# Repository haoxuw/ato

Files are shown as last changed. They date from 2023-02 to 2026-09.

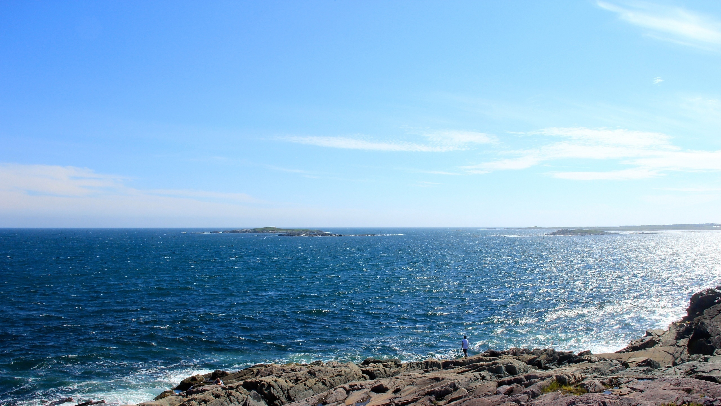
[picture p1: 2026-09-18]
urdf/method.jpg

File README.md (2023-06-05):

# ato

## What is this?

Simple Demo (https://www.youtube.com/watch?v=LdU0oIZtUVM)

See a video demo by clicking the above image.

Ato is an open-source robotic arm that can be built at home with a $200 budget.

## Demos

A 3 segments arm, visualized with dummy servo motors

Assembling a segment

A gripper with sockets to mount servo on its jaw

## Why design another arm

Many existing commercial robotic arms are robust, precise and packed with sensors. They are great, but their $10k~$100k price tag is also prohibitively expansive for the general public.

This arm is designed to be simple and inexpensive, by stacking modularized and interchangeable 3D printable segments. The first 4DoF arm cost around 120 CAD to build, including online orders and shipping costs (to Toronto) of standardized servos, nuts and bolts, and material costs of 3D printing, although excluding the cost for a Raspberry Pi or Arduino, and assumed access to a 3D printing facility or home printer.

A 6 Degrees-of-Freedom (DoF) arm may be built using 3 identical segments. A segment can be assembled by only three 3d printed objects: A bone and 2 mirrored halves of a joint.

Ato is competent for learning, or for proof of concept (PoC) projects. Although it's not built for heavy duty tasks, the 3D printed parts are fairly robust, and cost next to nothing to replace.

## What is in this repo

This repo is composed of 2 sub projects of ato:
 * Mesh: Allow you to build an arm: Modeling and configuration of 3D printable meshes
 * Control: Allow you to control an arm: Joint position space control using a PS4 controller for joint positions
 * ML-based control: Next steps
   * ML-based cartesian position
   * Full trajectories control

list of neat features
 * mesh:
   * Visualize printable STLs, and their compositional parts on a virtual shelf
 * control:
   * Joint space control
   * Cartesian space control using IK
   * Control with PS4 controller
   * Visualized arm simulation using matlab plots
   * Trajectory replay
 * learning -- deprecated due to performance issue
   * Training auto save, modify data/lr and continue
 ## Try it out!

For details visit the README.md in each project folder. Meanwhile here's a bird eye view.

### Build the arm

The arm would be assembled as illustrated:
arm_components_diagram

To manufacture the 3D Printable Structures, you have some options:

#### Download released mesh

STL files are available at the [resources branch](https://github.com/haoxuw/ato/tree/master-resources/printable_mesh).

Meanwhile the CD pipeline keeps the following STL in sync with master branch:
+ [Segment](https://printable-mesh.s3.us-east-2.amazonaws.com/master/SegmentAugmented_printable_mesh.stl)
+ [BoneSeparable](https://printable-mesh.s3.us-east-2.amazonaws.com/master/BoneSeparableVertical_printable_mesh.stl)
+ [BoneSeparablePitchOnly](https://printable-mesh.s3.us-east-2.amazonaws.com/master/pitch_only_BoneSeparableVertical_pitch_only__printable_mesh.stl)
+ [Gripper](https://printable-mesh.s3.us-east-2.amazonaws.com/master/GripperDragonWithServo_printable_mesh.stl)

You can also customize them, see details in ato_mesh/[README.md](https://github.com/haoxuw/ato/blob/master/ato_mesh/README.md)

### 3D print those mesh

Images to be added. Recommended settings to be added.

### Assembling the physical arm

Video to be added.

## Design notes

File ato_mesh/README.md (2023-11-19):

# mesh

## Build pre-defined arm

### Bill of materials (BOM)

### Download pre-defined mesh

STL files are available at the [resources branch](https://github.com/haoxuw/ato/tree/master-resources/printable_mesh).

### Make your customized mesh

Built on top of cadquery, the code in /mesh/ defines the 3D printable meshes of the arm, while strictly and literally practicing object oriented programming.

In case you may want to tweak the structural design, or configuration, such as to alter length or girth. Once your changes passes the continuous integration git actions pipeline (CI), it would be greatly appreciated if you would contribute back to this open source project via pull requests.

#### Make modifications

##### Installation

## Example commands to generate STL files

Tested under ubuntu 20+, python 3.9+, see examples in `ci.yaml`.

### Prerequisites

* python 3.9+
* if first time running, no folder called ./ato_mesh/venv (the script would create).

### Generate STL files

> $ ./ato_mesh/scripts/generate_shelf.sh --export -o ./generated

You sure see logs printed to console as color green. The .stl files would be located under `./ato_mesh/generated/`

## Code architecture

### High-level walk through

To configure an segment with customized length girth etc. Define a new class under segment_configuration.py . Functionality of the variables are [illustrated here](https://github.com/haoxuw/ato/blob/master-resources/images/illustrations/segment_config_diagram.png)
### Naming conventions

## Demo

### Build

### Alternatives
While it's a bad idea, in theory, one may build a theoretical 10-segment arm

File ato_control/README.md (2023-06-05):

# Contorller Manual

This section describes how to control the arm.

## Get Started

### Prerequisites

1. Activate venv and install dependencies
2. If using PS4 controller, connect to bluetooth. Some hardware doesn't work well with Raspberry Pi OS, you may try to connect by holding `Share` + `PS` button.

### Start the Controller
```
./scripts/activate_arm.sh
```

The PS4 controller signals are updated by `/dev/input/js*` on ubuntu. This script would try connect to the lastest connected joystick device. To specify a target input device, e.g. js6, use `./ato_control/scripts/activate_arm.sh -j 6`

## Using a PS4 controller

### Short Story

* 2 Joysticks to control 2 segments, `L1 R1` to swtich targeted segments.
* `L2 R2` to control gripper.
* `Share` to `enable` detailed logging, `Option` to disconnect.
* `Arrow keys` to switch modes.
* `L3` (press left joystick) move to Home positions.
* `R3` to replay a saved trajectory.

### Long Story

Each mode is mapped to an arrow key, via
```
def __update_input_states(self, key, value):
  ...
def __controller_mode_to_button_mapping(self):
  ...
```

Results in mapping:
```
{
    UP: IN_CARTESIAN_MODE,
    RIGHT: IN_JOINT_SPACE_MODE,
    DOWN: IN_SETTING_MODE,
    LEFT: IN_TRAJECTORY_EDITING_MODE,
}
```

## Modes

The controller can be in one of four possible modes, defined by:

```
def controller_modes(self):.
 - IN_CARTESIAN_MODE
   - Under development and disabled -- limited functionality with preformings to be improved
 - IN_JOINT_SPACE_MODE
   - Control each servo motor individually
 - IN_SETTING_MODE
   - Calibrating between physical and logical position of motors, change velocity
 - IN_TRAJECTORY_EDITING_MODE
   - To create a trajectory, either by setting waypoints and pauses, or recording one live.
"""
```

#### IN_CARTESIAN_MODE

Disabled, currently under development, sorry.

#### IN_JOINT_SPACE_MODE

Left joystick to control the 1st segment, right for the 2nd. Pushing vertically for roll, horizontally for pitch.

Press R1, so that left for the 2nd, right for the 3rd. Press again for 3rd and 4th. Press L1 to reverse. 

#### IN_SETTING_MODE

Mainly used for advanced calibration.

#### IN_TRAJECTORY_EDITING_MODE

* `L3` save the trajectory in editting, and reset_trajectory_in_editing buffer
* `Circle (O)` reset_trajectory_in_editing buffer
* `Cross (X)` append the current position as waypoint
* `Triagle` append a pause
* `Square` toggle trajectory segment recording, each segment would be appended to trajectory in editting

## Using a Kyeboard

To be implemented.

# Software Architecture

This package uses the following components to implement control flow of the arm

-- root obj of arm: ArmController
  -- contains: Ps4Joystick
  -- contains: RaspberryPi
  -- contains multiple: ServoInterface
      -- each has reference to the RaspberryPi

## More Example Commands

#### Start arm controller without connecting to RPI and also enable visualization
> $ ./ato_control/scripts/activate_arm.sh

#### To start arm controller to interface with RaspberryPI (RPI), with joystick at /dev/input/js0 (-j 0)
> $ ./ato_control/scripts/activate_arm.sh -j 0

#### If you have ros installed, you can examine the URDF models by

> $ sudo apt-get install libatlas-base-dev -y
> $ ./ato_control/scripts/download_urdf_mesh_stl.sh && roslaunch urdf_tutorial display.launch model:=./urdf/ato_3_seg_270_deg.urdf

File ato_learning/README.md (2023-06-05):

# This package is currently deprecated due to performance issue

# Prerequisites

## Install Cuda GPU support
e.g.

```
$ sudo apt install nvidia-cuda-toolkit
$ sudo apt purge nvidia-*
$ sudo add-apt-repository ppa:graphics-drivers/ppa
$ sudo apt update
$ sudo apt install nvidia-470
```

## Example commands to train inverse kinematics

### Generate training data with the control package
> $ ./ato_control/scripts/activate_arm.sh --generate_training_data 1000000 --training_data_filepath_prefix ~/.ato/training_data

### Start training using the data generated above
> $ ./ato_learning/scripts/training.sh --training_data_filepath_prefix ~/.ato/training_data --max_epochs 256 --depth 12 --width 256 --new_ik

### you can kill the above process anytime, and resume training by
> $ ./ato_learning/scripts/training.sh --training_data_filepath_prefix ~/.ato/training_data --max_epochs 256 --depth 12 --width 256 --fit_ik

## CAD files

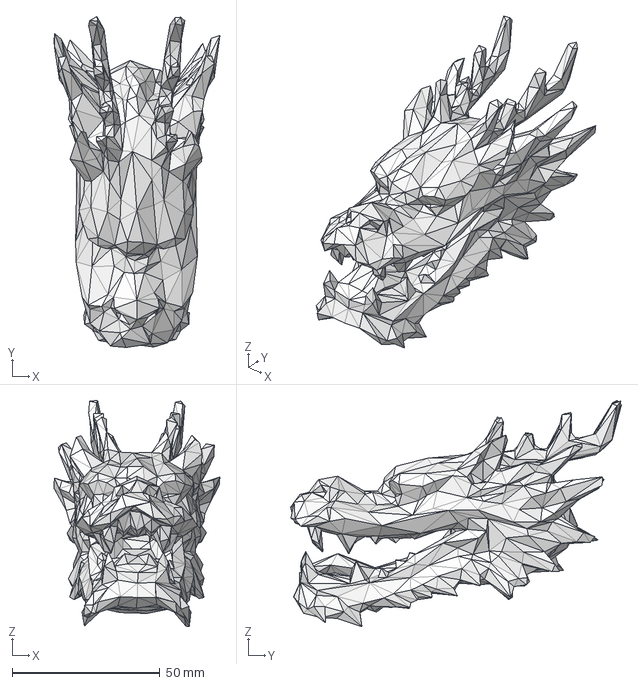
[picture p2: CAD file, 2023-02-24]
ato_mesh/mesh/model_structure/gripper/dragon_head.step
56.1 x 111.9 x 76.5 mm

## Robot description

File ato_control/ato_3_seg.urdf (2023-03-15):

<robot name="ato">
  <link name="base_link">
    <visual>
      <origin rpy="0 0 0" xyz="0 0 0"/>
      <geometry>
      <mesh filename="file:///tmp/BoneAugmented_urdf_mesh.stl"/>
      </geometry>
    </visual>
  </link>

  <joint name="base_link_to_joint_1" type="revolute">
    <axis xyz="0 0 1"/>
    <limit lower="-1.5708" upper="3.14159" effort="1.0" velocity="1.0"/>
    <parent link="base_link"/>
    <child link="joint_1"/>
    <origin xyz="0 0 0" rpy="0 0 0"/>
  </joint>

  <link name="joint_1">
    <visual>
      <origin rpy="0 0 0" xyz="0 0 0"/>
      <geometry>
      <mesh filename="file:///tmp/JointAugmented_urdf_mesh.stl"/>
      </geometry>
    </visual>
  </link>

  <joint name="joint_1_to_bone_1" type="revolute">
    <axis xyz="1 0 0"/>
    <limit lower="-2.26893" upper="2.26893" effort="1.0" velocity="1.0"/>
    <parent link="joint_1"/>
    <child link="bone_1"/>
    <origin xyz="0 0 220" rpy="0 0 0"/>
  </joint>

  <link name="bone_1">
    <visual>
      <origin rpy="0 0 0" xyz="0 0 0"/>
      <geometry>
      <mesh filename="file:///tmp/BoneAugmented_urdf_mesh.stl"/>
      </geometry>
    </visual>
  </link>

  <joint name="bone_1_to_joint_2" type="revolute">
    <axis xyz="0 0 1"/>
    <limit lower="-1.5708" upper="3.14159" effort="1.0" velocity="1.0"/>
    <parent link="bone_1"/>
    <child link="joint_2"/>
    <origin xyz="0 0 0" rpy="0 0 0"/>
  </joint>

  <link name="joint_2">
    <visual>
      <origin rpy="0 0 0" xyz="0 0 0"/>
      <geometry>
      <mesh filename="file:///tmp/JointAugmented_urdf_mesh.stl"/>
      </geometry>
    </visual>
  </link>

  <joint name="joint_2_to_bone_2" type="revolute">
    <axis xyz="1 0 0"/>
    <limit lower="-2.26893" upper="2.26893" effort="1.0" velocity="1.0"/>
    <parent link="joint_2"/>
    <child link="bone_2"/>
    <origin xyz="0 0 220" rpy="0 0 0"/>
  </joint>

  <link name="bone_2">
    <visual>
      <origin rpy="0 0 0" xyz="0 0 0"/>
      <geometry>
      <mesh filename="file:///tmp/BoneAugmented_urdf_mesh.stl"/>
      </geometry>
    </visual>
  </link>

  <joint name="bone_2_to_joint_3" type="revolute">
    <axis xyz="0 0 1"/>
    <limit lower="-1.5708" upper="3.14159" effort="1.0" velocity="1.0"/>
    <parent link="bone_2"/>
    <child link="joint_3"/>
    <origin xyz="0 0 0" rpy="0 0 0"/>
  </joint>

  <link name="joint_3">
    <visual>
      <origin rpy="0 0 0" xyz="0 0 0"/>
      <geometry>
      <mesh filename="file:///tmp/JointAugmented_urdf_mesh.stl"/>
      </geometry>
    </visual>
  </link>

  <joint name="joint_3_to_bone_3" type="revolute">
    <axis xyz="1 0 0"/>
    <limit lower="-2.26893" upper="2.26893" effort="1.0" velocity="1.0"/>
    <parent link="joint_3"/>
    <child link="bone_3"/>
    <origin xyz="0 0 220" rpy="0 0 0"/>
  </joint>

  <link name="bone_3">
    <visual>
      <origin rpy="0 0 0" xyz="0 0 0"/>
      <geometry>
      <mesh filename="file:///tmp/GripperDragonWithServo_urdf_mesh.stl"/>
      </geometry>
    </visual>
  </link>

  <joint name="bone_3_to_endeffector" type="fixed">
    <parent link="bone_3"/>
    <child link="endeffector_link"/>
    <origin xyz="0 0 147" rpy="0 0 0"/>
  </joint>

  <link name="endeffector_link">
    <visual>
      <origin rpy="0 0 0" xyz="0 0 0"/>
      <geometry>
       <box size="1 2 3"/>
      </geometry>
    </visual>
  </link>
</robot>

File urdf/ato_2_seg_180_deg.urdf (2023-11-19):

<robot name="ato">
  <link name="bone_0">
    <visual>
      <origin rpy="0 0 0" xyz="0 0 0"/>
      <geometry>
      <mesh filename="file:///tmp/pitch_range_180/BoneAugmented_urdf_mesh.stl"/>
      </geometry>
    </visual>
    <inertial>
      <mass value="0.0"/>
      <inertia ixx="0.0" ixy="0.0" ixz="0.0" iyy="0.0" iyz="0.0" izz="0.0"/>
    </inertial>
  </link>

  <joint name="bone_0_to_joint_1" type="revolute">
    <axis xyz="0 0 1"/>
    <limit lower="-1.5708" upper="1.5708" effort="1.0" velocity="1.0"/>
    <parent link="bone_0"/>
    <child link="joint_1"/>
    <origin xyz="0 0 0" rpy="0 0 0"/>
  </joint>

  <link name="joint_1">
    <visual>
      <origin rpy="0 0 0" xyz="0 0 0"/>
      <geometry>
      <mesh filename="file:///tmp/pitch_range_180/JointAugmented_urdf_mesh.stl"/>
      </geometry>
    </visual>
  </link>

  <joint name="joint_1_to_bone_1" type="revolute">
    <axis xyz="1 0 0"/>
    <limit lower="-1.48353" upper="1.48353" effort="1.0" velocity="1.0"/>
    <parent link="joint_1"/>
    <child link="bone_1"/>
    <origin xyz="0 0 200" rpy="0 0 0"/>
  </joint>

  <link name="bone_1">
    <visual>
      <origin rpy="0 0 0" xyz="0 0 0"/>
      <geometry>
      <mesh filename="file:///tmp/pitch_range_180/BoneAugmented_urdf_mesh.stl"/>
      </geometry>
    </visual>
  </link>

  <joint name="bone_1_to_joint_2" type="revolute">
    <axis xyz="0 0 1"/>
    <limit lower="-1.5708" upper="1.5708" effort="1.0" velocity="1.0"/>
    <parent link="bone_1"/>
    <child link="joint_2"/>
    <origin xyz="0 0 0" rpy="0 0 0"/>
  </joint>

  <link name="joint_2">
    <visual>
      <origin rpy="0 0 0" xyz="0 0 0"/>
      <geometry>
      <mesh filename="file:///tmp/pitch_range_180/JointAugmented_urdf_mesh.stl"/>
      </geometry>
    </visual>
  </link>

  <joint name="joint_2_to_endeffector" type="revolute">
    <axis xyz="1 0 0"/>
    <limit lower="-1.48353" upper="1.48353" effort="1.0" velocity="1.0"/>
    <parent link="joint_2"/>
    <child link="endeffector"/>
    <origin xyz="0 0 200" rpy="0 0 0"/>
  </joint>

  <link name="endeffector">
    <visual>
      <origin rpy="0 0 0" xyz="0 0 0"/>
      <geometry>
      <mesh filename="file:///tmp/pitch_range_180/GripperDragonWithServo_urdf_mesh.stl"/>
      </geometry>
    </visual>
  </link>

  <joint name="endeffector_to_dummy_object" type="revolute">
    <axis xyz="1 0 0"/>
    <limit lower="0" upper="0" effort="1.0" velocity="1.0"/>
    <parent link="endeffector"/>
    <child link="dummy_object_link"/>
    <origin xyz="0 0 147" rpy="0 0 0"/>
  </joint>

  <link name="dummy_object_link">
    <visual>
      <origin rpy="0 0 0" xyz="0 0 0"/>
      <geometry>
       <box size="1 2 3"/>
      </geometry>
    </visual>
  </link>
</robot>

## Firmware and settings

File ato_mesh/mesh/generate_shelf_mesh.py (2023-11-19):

# This software is forever free for personal and educational usage,

# Copyright (c) 2023, ATOBOT CORP. (1000399600) and/or its affiliates,
# distributed under a multi-licensing model, available for Proprietary and GPL.

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
import argparse
import logging

from mesh.configuration import arm_configuration, segment_configuration
from mesh.cq_lib import cq_mesh_shelf
from mesh.model_structure.arm import arm, mount
from mesh.model_structure.gripper import (
    gripper_dragon_with_servo,
    gripper_tri_sticks_with_servo,
)
from mesh.model_structure.mechanical_parts import (
    allocated_motors,
    bolt,
    horn_arm_25T,
    horn_disk_ds5160,
    horn_disk_nema17,
    motor_servo,
    motor_stepper,
)
from mesh.model_structure.segment import (
    bone_augmented,
    bone_separable,
    bone_separable_vertical,
    joint_augmented,
    segment_augmented,
)
from mesh.model_structure.segment.abstractions import (
    bone_abstract,
    joint_abstract,
    segment_abstract,
)
from mesh.model_structure.toys import gripper_dragon_on_wheels, wheels


def get_args():
    parser = argparse.ArgumentParser()
    parser.add_argument(
        "--abstract",
        action="store_true",
        help="If only print the abstract objects, this would remove functional components such as bolt sockets, motor holder etc.",
    )
    parser.add_argument(
        "--pitch_range_180",
        action="store_true",
        help="If generate joints with pitch ranges of 0~180 or 0~270",
    )
    parser.add_argument(
        "--joint_polygon_sides",
        type=int,
        default=-1,
        help="If generate polygon joint, round if -1",
    )
    parser.add_argument(
        "--all", action="store_true", help="If export all models on shelf"
    )
    parser.add_argument(
        "--no_default",
        action="store_true",
        help="If not to print the default printable models, which includes a complete segment, separable bone, and gripper",
    )
    parser.add_argument(
        "--toys", action="store_true", help="If print the random selection of odd toys"
    )
    parser.add_argument("--bolt", action="store_true", help="If print bolt")
    parser.add_argument("--gripper", action="store_true", help="If print gripper")
    parser.add_argument("--motor", action="store_true", help="If print motor")
    parser.add_argument("--parts", action="store_true", help="If print whole")
    parser.add_argument("--bone", action="store_true", help="If print bone")
    parser.add_argument("--mount", action="store_true", help="If print mount")
    parser.add_argument(
        "--arm_include_motor_mesh",
        action="store_true",
        help="If print an assembled arm with motor_mesh",
    )
    parser.add_argument("--stepper", action="store_true")
    parser.add_argument("--servo", action="store_true")
    parser.add_argument("--arm", action="store_true", help="If print an assembled arm")

    parser.add_argument(
        "--arm10", action="store_true", help="If print an assembled 10-segment arm"
    )
    parser.add_argument(
        "--cylinder", action="store_true", help="If use cylinder roll holder"
    )
    parser.add_argument(
        "--separable_bone", action="store_true", help="If generate separable bone"
    )
    parser.add_argument(
        "--separable_bone_pitch_only",
        action="store_true",
        help="If only generate pitch separable bone",
    )
    parser.add_argument(
        "--gripper_servo_use_shaft_bolt",
        action="store_true",
        help="If generate installation space for a shaft bolt for the gripper",
    )
    parser.add_argument(
        "--tighten_bolt_socket",
        action="store_true",
        help="If print bolt socket that are smaller than bolt diameter, so that it the helix screws into the model.",
    )
    parser.add_argument(
        "--nozzle_diameter",
        type=float,
        default=0.4,
        help="The nozzle diameter used for 3D printing. This value will be used in asserts, to make sure intentional gaps are appropriate in relations to nozzle diameter.",
    )
    parser.add_argument(
        "--horn_bolt_length_override",
        type=int,
        default=None,
        help="If use a specified horn_bolt_length",
    )
    parser.add_argument(
        "--bone_length",
        type=int,
        default=57,
        help="Defaults bone length.",
    )
    parser.add_argument(
        "--export", action="store_true", help="If export printable models on shelf"
    )
    parser.add_argument(
        "--export_all", action="store_true", help="If export all models on shelf"
    )
    parser.add_argument(
        "-o",
        "--out_dir",
        dest="out_dir",
        type=str,
        default="./generated",
        help="Where to put the generated resources",
    )
    parser.add_argument(
        "--no_axes",
        action="store_true",
        help="If not visualize axes (distinguished by length X:1 Y:2 Z:3)",
    )
    parser.add_argument(
        "--no_shelf",
        action="store_true",
        help="If not visualize shelf (i.e. collection of all the mesh)",
    )
    return parser.parse_args()


def add_models(cq_meshes, args):
    logging.info("Adding models to shelf for display and export...")
    if not args.stepper or args.servo:
        actuator_type = segment_configuration.MotorType.SERVO
    else:
        actuator_type = segment_configuration.MotorType.STEPPER

    segment_configs = segment_configuration.SegmentConfigs(
        bone_length=args.bone_length,
        actuator_type=actuator_type,
        joint_polygon_sides=args.joint_polygon_sides,
        pitch_range_180=args.pitch_range_180,
        nozzle_diameter=args.nozzle_diameter,
        roll_bone_holder_type=segment_configuration.RollBoneHolderType.CYLINDER
        if args.cylinder
        else segment_configuration.RollBoneHolderType.SPHERE,
        separable_bone=args.separable_bone,
        separable_bone_pitch_only=args.separable_bone_pitch_only,
        BoltSocketDiamTightenFactor=0.90 if args.tighten_bolt_socket else 1,
        HornBoltLengthOverride=args.horn_bolt_length_override,
        gripper_servo_use_shaft_bolt=args.gripper_servo_use_shaft_bolt,
    )
    if args.all or args.bolt:
        cq_meshes += [
            bolt.Bolt(
                segment_configs=segment_configs,
                install_from_side_instead_along=True,
                bolt_configs=segment_configuration.BoltConfigsBase(
                    BoltDiam=3, BoltLength=16
                ),
            )
        ]
    if args.all or args.motor:
        if actuator_type == segment_configuration.MotorType.SERVO:
            cq_meshes += [
                # pitch
                motor_servo.ServoMotor(
                    segment_configs=segment_configs,
                    install_from_side_instead_along=True,
                    horn_mesh_class=horn_disk_ds5160.HornDiskDs5160,
                    motor_configs=segment_configuration.ServoConfigsDs5160(),
                ),
                # roll
                motor_servo.ServoMotor(
                    segment_configs=segment_configs,
                    install_from_side_instead_along=False,
                    horn_mesh_class=horn_disk_ds5160.HornDiskDs5160,
                    motor_configs=segment_configuration.ServoConfigsDs5160(),
                ),
                # gripper
                motor_servo.ServoMotor(
                    segment_configs=segment_configs,
                    install_from_side_instead_along=False,
                    horn_mesh_class=horn_arm_25T.HornArm25T,
                    motor_configs=segment_configuration.ServoConfigsDs3218(),
                    generate_motor_fastening_bolt_space=True,
                ),
                allocated_motors.AllocatedMotors(segment_configs=segment_configs),
            ]
        elif actuator_type == segment_configuration.MotorType.STEPPER:
            cq_meshes += [
                motor_stepper.StepperMotor(
                    segment_configs=segment_configs,
                    install_from_side_instead_along=True,
                    horn_mesh_class=horn_disk_nema17.HornDiskNema17,
                ),
                motor_stepper.StepperMotor(
                    segment_configs=segment_configs,
                    install_from_side_instead_along=False,
                    horn_mesh_class=horn_disk_nema17.HornDiskNema17,
                ),
            ]
    if args.all or args.gripper:
        cq_meshes += [
            # gripper_dragon_with_servo.GripperDragonWithServo(
            #     segment_configs=segment_configs
            # )
            gripper_tri_sticks_with_servo.GripperTriSticksWithServo(
                segment_configs=segment_configs
            )
        ]
    if args.all or args.parts:
        cq_meshes += [
            bone_separable.BoneSeparable(segment_configs=segment_configs),
            joint_augmented.JointAugmentedPos(segment_configs=segment_configs),
            joint_augmented.JointAugmentedNeg(segment_configs=segment_configs),
        ]
    if args.all or args.bone:
        cq_meshes += [
            bone_separable.BoneSeparable(segment_configs=segment_configs),
            bone_separable_vertical.BoneSeparableVertical(
                segment_configs=segment_configs
            ),
        ]
    if args.all or args.mount:
        cq_meshes += [
            mount.MountCombined(segment_configs=segment_configs),
        ]
    if args.all or args.abstract:
        cq_meshes += [
            bone_abstract.BoneAbstract(segment_configs=segment_configs),
            joint_abstract.JointAbstract(segment_configs=segment_configs),
            joint_abstract.JointAbstractPos(segment_configs=segment_configs),
            joint_abstract.JointAbstractNeg(segment_configs=segment_configs),
            segment_abstract.SegmentAbstract(segment_configs=segment_configs),
        ]
    if args.all or args.toys:
        cq_meshes += [
            wheels.Wheels(),
            gripper_dragon_on_wheels.GripperDragonOnWheels(
                segment_configs=segment_configs
            ),
        ]
    if args.all or args.arm:
        cq_meshes += [
            arm.Arm(
                name="4Segments",
                arm_configs=arm_configuration.ArmConfigsBase4Segments(),
                include_motor_mesh=args.arm_include_motor_mesh,
            ),
            arm.Arm(
                name="3Segments",
                arm_configs=arm_configuration.ArmConfigsBase3Segments(),
                include_motor_mesh=args.arm_include_motor_mesh,
            ),
            arm.Arm(
                name="2SegmentHalfJoint",
                arm_configs=arm_configuration.ArmConfigsBase2Segment(),
                half_joint=True,
                include_motor_mesh=True,
            ),
            arm.Arm(
                name="1Segment",
                arm_configs=arm_configuration.ArmConfigsBase1Segment(),
                half_joint=False,
                include_motor_mesh=True,
            ),
            arm.Arm(
                name="1SegmentHalfJoint",
                arm_configs=arm_configuration.ArmConfigsBase1Segment(),
                half_joint=True,
                include_motor_mesh=True,
            ),
        ]
    if args.arm10:
        cq_meshes += [
            arm.Arm(
                name="10Segments",
                arm_configs=arm_configuration.ArmConfigsBase10Segments(),
                include_motor_mesh=args.arm_include_motor_mesh,
            )
        ]
    if args.all or not args.no_default:
        cq_meshes += [
            segment_augmented.SegmentAugmented(segment_configs=segment_configs),
            joint_augmented.JointAugmented(segment_configs=segment_configs),
            bone_augmented.BoneAugmented(segment_configs=segment_configs),
            gripper_dragon_with_servo.GripperDragonWithServo(
                segment_configs=segment_configs
            ),
            bone_separable_vertical.BoneSeparableVertical(
                segment_configs=segment_configs,
                separable_bone_pitch_only=True,
                name="pitch_only",
            ),
        ]
    return cq_meshes


def generate_mesh_shelf():
    args = get_args()

    cq_meshes = add_models(cq_meshes=[], args=args)

    shelf = cq_mesh_shelf.CqMeshShelf(
        cq_meshes=reversed(cq_meshes),
        distance=400,
        show_axes=not args.no_axes,
        out_dir=args.out_dir,
    )

    if args.export:
        shelf.export_each(only_printable_or_urdf=not args.export_all)
    if not args.no_shelf:
        shelf.export()


if __name__ == "__main__":
    generate_mesh_shelf()

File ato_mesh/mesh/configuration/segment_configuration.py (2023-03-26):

# This software is forever free for personal and educational usage,

# Copyright (c) 2023, ATOBOT CORP. (1000399600) and/or its affiliates,
# distributed under a multi-licensing model, available for Proprietary and GPL.

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
import logging
from dataclasses import dataclass
from typing import Tuple


@dataclass
class MotorType:
    STEPPER = "Stepper Motor"
    SERVO = "Servo Motor"


@dataclass
class MotorHornType:
    DISK = "Disk Horn"
    ARM = "Arm Horn"


@dataclass
class RollBoneHolderType:
    SPHERE = "Sphere"
    CYLINDER = "Cylinder"
    NONE = "Do Not Generate"


# since this project is named ATO(mic), let's name the first build (Silicon)
# The Si180 version supports 180 degree pitch range, the 270 version supports 270 degrees, while requiring a longer joint
@dataclass
class StructuralConfigsSi180:
    # to understand the what those variables represent, please refer to
    # https://github.com/haoxuw/ato/blob/master-resources/images/illustrations/segment_config_diagram.png
    # length units are in mm:

    ##########################################
    ## values derived, to be assigned in __init__
    BoneLength: float
    PitchBoneMeshNetLength: float
    RollBoneMeshNetLength: float
    SegmentLength: float
    ##########################################

    ##########################################
    ## values hard-coded to best fit the Ds5160 Servo and its HornDisk geometry:
    JointRadius: float = 33
    BoneRadius: float = 16.5

    # Used as value to represent "far away coordinates", but not too far, so we can still visualize
    Far: float = 142
    VeryFar: float = Far * 10
    ##########################################

    ##########################################
    ## values that are configurable:
    JointLength: float = 110
    PitchRange: float = 180
    MotorTopLocation: float = 70

    PitchMotorOffsetX: float = 25  # larger is outwards
    PitchCenterLocationZ: float = (
        0  # 0: pitch axis is aligned with joint sphere's center, z: move inwards z mm
    )
    ##########################################

    BoneHolderRadius: float = BoneRadius * 1.4

    # RotateHolder is what locks roll bone in the joint, which allows rotation
    # When set to sphere, breath = radius
    # When set to cylinder, depth measures furthest point of holder to bone, i.e. depth = CylinderRadius - BoneRadius
    # meanwhile breath measures height of the cylinder
    # those values/ratio are set arbitrarily
    RollCylinderHolderDepth: float = BoneHolderRadius - BoneRadius
    RollCylinderHolderBreadth: float = BoneHolderRadius

    # when RollHolderOffsetZ == 0 the holder's edge would be touching roll motor
    # this offset move the holder outwards
    RollHolderOffsetZ: float = 15

    RollLubricantOpeningWidth: float = BoneHolderRadius

    # coefficients are empirical, and was used to calculate offsets of the bolts binding two pats of the joints
    BoltOffsetCoefficientX: float = 1.58  # less is outwards
    BoltOffsetCoefficientZTop: float = 1.74  # less is upwards
    BoltOffsetCoefficientZDown: float = 1.74  # less is downwards

    SurfaceGive: float = 0.3
    MountUnitSize: float = 90

    JointSphereHolders = [
        (
            (
                BoneRadius + RollCylinderHolderDepth * 1.4,
                0,
                MotorTopLocation + RollHolderOffsetZ / 2,
            ),
            5,
        ),
        (
            (
                -BoneRadius - RollCylinderHolderDepth * 1.4,
                0,
                MotorTopLocation + RollHolderOffsetZ / 2,
            ),
            5,
        ),
        (
            (
                (BoneRadius + RollCylinderHolderDepth + JointRadius) / 2,
                0,
                BoneRadius * 4 / 5,
            ),
            3,
        ),
        (((BoneRadius + RollCylinderHolderDepth + JointRadius) / 2, 0, 0), 3),
    ]  # offset_x, offset_y, radius

    def __init__(
        self, bone_length: float, roll_bone_holder_type: RollBoneHolderType
    ) -> None:
        # <BoneLength> measures the net length of bones visible and functional
        # this is because a section of roll bone is always inside of the joint
        # length of that portion depends on length of joint and location of motor
        # so the printed bone is longer than bone_length
        self.BoneLength = bone_length
        self.PitchBoneMeshNetLength = self.JointRadius
        self.RollBoneMeshNetLength = (
            self.BoneLength + self.JointRadius * 2 - self.PitchBoneMeshNetLength
        )

        self.RollBoneHolderType = roll_bone_holder_type
        self.SegmentLength = (
            self.BoneLength
            + self.JointRadius
            + self.JointLength
            - self.PitchCenterLocationZ
        )  # == RollBoneEdgeToPitchCenterLocation
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

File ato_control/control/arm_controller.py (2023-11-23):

# This software is forever free for personal and educational usage,

# Copyright (c) 2023, ATOBOT CORP. (1000399600) and/or its affiliates,
# distributed under a multi-licensing model, available for Proprietary and GPL.

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
import copy
import json
import logging
import math
import numbers
import os
import pathlib
import threading
import time
from datetime import datetime
from typing import Dict, Tuple

import matplotlib.pyplot as plt
import numpy as np
import pinocchio
import pybullet
from control import arm_position, arm_trajectory, ps4_joystick, raspberry_pi
from control.config_and_enums.arm_connection_config import (
    ActuatorPurpose,
    ArmConnectionAttributes,
    ServoConnectionConfig,
)
from control.config_and_enums.controller_enums import ControllerStates
from control.interface_classes import servo_interface
from matplotlib.animation import FuncAnimation
from pinocchio import robot_wrapper
from scipy.spatial.transform import Rotation


class ArmController:
    def __init__(
        self,
        pi_obj: raspberry_pi.RaspberryPi,
        joystick_obj: ps4_joystick.Ps4Joystick,
        arm_segments_config: Dict[Tuple[int, str], ServoConnectionConfig],
        frame_rate=100,
        auto_save_controller_states_to_file=True,
        actuator_velocities_deg_per_ms=tuple(
            i * 0.02 for i in range(1, 10)
        ),  # angular velocity
        cartesian_velocities_mm__per_ms=tuple(i * 0.03 for i in range(1, 10)),
        initial_velocity_level=3,
        home_folder_path="~/.ato/",
    ):
        self._input_states = None
        assert isinstance(pi_obj, raspberry_pi.RaspberryPi)
        self.__pi_obj = pi_obj

        assert isinstance(joystick_obj, ps4_joystick.Ps4Joystick)
        self.__joystick_obj = joystick_obj
        self.__joystick_obj.connect_arm_controller(self)

        self._indexed_servo_names: Tuple[str]
        self._indexed_servo_objs: Tuple[servo_interface.ServoInterface]
        self._indexed_servo_configs: Tuple[ServoConnectionConfig]
        self._indexed_segment_lengths: Tuple[float]
        self._gripper_length: float

        (
            self._indexed_servo_names,
            self._indexed_servo_objs,
            self._indexed_servo_configs,
            self._indexed_segment_lengths,
            self._gripper_length,
            self.__actuator_indices_mapping,
            self.__gripper_index_mapping,
            self.num_segments,
        ) = ArmController.__register_servo_objs(
            arm_segments_config=arm_segments_config, pi_obj=self.pi_obj
        )

        self.home_positions = self.__initialize_home_positions(
            num_segments=self.num_segments
        )

        self._inverse_indexed_servo_names = {
            name: index for index, name in enumerate(self._indexed_servo_names)
        }

        arm_position.ActuatorPositions.set_arm_segment_lengths(
            arm_segment_lengths=self._indexed_segment_lengths
        )
        arm_position.ActuatorPositions.set_actuator_indices_mapping(
            actuator_indices_mapping=self.__actuator_indices_mapping
        )
        arm_position.ActuatorPositions.set_gripper_length(
            gripper_length=self._gripper_length
        )
        arm_position.ActuatorPositions.set_gripper_index_mapping(
            gripper_index_mapping=self.__gripper_index_mapping
        )
        arm_position.ActuatorPositions.set_rotation_ranges(
            rotation_ranges=self._get_indexed_rotation_ranges()
        )

        current_dir = pathlib.Path(__file__).parent
        self.urdf_filename = os.path.join(
            current_dir,
            "..",
            "..",
            "urdf",
            arm_segments_config[ArmConnectionAttributes.URDF_FILENAME],
        )

        try:
            self.robot: pinocchio.robot_wrapper.RobotWrapper = (
                robot_wrapper.RobotWrapper.BuildFromURDF(self.urdf_filename)
            )  # Add pinocchio wrapper
        except Exception as e:
            logging.warning(
                f"Failed to load robot from urdf_filename: {self.urdf_filename}, {e}"
            )
            logging.warning(f"Inverse kinematics will not be available.")
            self.robot = None

        self.frame_rate = frame_rate
        self.interval_ms = 1000 // frame_rate

        self.__auto_save_controller_states_to_file = auto_save_controller_states_to_file

        self.__controller_thread = None
        self.__to_stop_clock = False
        self.__to_stop_visualization = False
        self.__segment_id_pointer = 0

        # velocity settings
        self.__actuator_velocities_deg_per_ms = actuator_velocities_deg_per_ms
        self.__cartesian_velocities_mm__per_ms = cartesian_velocities_mm__per_ms
        self.__velocity_level = initial_velocity_level

        # trajectory replay (joint space)
        self.__trajectory_saved: arm_trajectory.TrajectoryActuatorPositions = None
        self.__trajectory_to_play: arm_trajectory.ArmTrajectory = None

        # joint space control: tracks current position of actuators
        self.__current_actuator_position_obj = None
        self.__current_robot_pose_detail = None
        self.__current_endeffector_pose = None

        self.__positions_momentum = None

        # cartesian space control, tracks:
        # where is the intended pose
        self._intended_pose: arm_position.EndeffectorPose = None
        # where is the (realistic) attempted pose (best effort towards the intended pose, because not all pose are reachable)
        # self.__attempted_pose: motion.EndeffectorPose = None
        # where is the attempted joint positions == IK(attempted pose)
        # self.__attempted_joint_positions: motion.ActuatorPositions = None
        # where is the current joint positions, max velocity may not keep up achieving the attempted
        # is self.__current_actuator_position_obj

        self.reset_input_states()
        self.reset_controller_flags()
        self.reset_trajectory_in_editing()

        self.load_controller_states()
        self.__update_intended_pose_to_current_pose()

        self._home_folder_path = home_folder_path
        self.create_folder(folder_path=home_folder_path)

        self.__controller_start_time = datetime.now()
        self.ready = True

    def __del__(self):
        try:
            pybullet.disconnect()
        except Exception as e:
            logging.warning(f"Failed to disconnect pybullet, exception: {e}")

    def reset_input_states(self):
        # to be override
        return

    @staticmethod
    def create_folder(folder_path):
        folder_path = os.path.expanduser(folder_path)
        pathlib.Path(folder_path).mkdir(parents=True, exist_ok=True)

    @property
    def is_at_home_positions(self):
        return np.allclose(
            self.home_positions,
            self.__fetch_indexed_actuator_positions(),
            rtol=0.001,
        )  # 0.1% tolerance

    def get_input_states(self):
        return self._input_states
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

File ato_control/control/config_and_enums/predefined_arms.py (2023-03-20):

# This software is forever free for personal and educational usage,

# Copyright (c) 2023, ATOBOT CORP. (1000399600) and/or its affiliates,
# distributed under a multi-licensing model, available for Proprietary and GPL.

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

from control.config_and_enums.arm_connection_config import (
    ActuatorPurpose,
    ArmConnectionAttributes,
    PiHeaderIdToBCM,
    ServoConnectionConfig,
)
from control.servo_ds3218 import ServoDs3218
from control.servo_ds5160 import ServoDs5160

# this object defines the particular arm config that I happen to be using now

# Copied from the StructuralConfigsSi's configuration when generating mesh
SegmentLength = 220
GripperLength = 147
# servo_max_position should be configured according to which flavor of the arm was assembled
# use (-130, 130) instead of (0, 270) on rotation_range to prevent damages from overshooting rotation
arm_6_axis = {
    ArmConnectionAttributes.ARM_NAME: "ARM_6_AXIS_270_DEG",
    ArmConnectionAttributes.URDF_FILENAME: "ato_3_seg_270_deg.urdf",
    0: {
        ArmConnectionAttributes.PHYSICAL_LENGTH: SegmentLength,
        ActuatorPurpose.ROLL: ServoConnectionConfig(
            (
                ActuatorPurpose.ROLL,
                PiHeaderIdToBCM.TWENTY_NINE,
                ServoDs5160,
                270,
                1,
                (-135, 135),
            ),
        ),
        ActuatorPurpose.PITCH: ServoConnectionConfig(
            (
                ActuatorPurpose.PITCH,
                PiHeaderIdToBCM.THIRTY_ONE,
                ServoDs5160,
                270,
                1,
                (-130, 130),
            )
        ),
    },
    1: {
        ArmConnectionAttributes.PHYSICAL_LENGTH: SegmentLength,
        ActuatorPurpose.ROLL: ServoConnectionConfig(
            (
                ActuatorPurpose.ROLL,
                PiHeaderIdToBCM.THIRTY_TWO,
                ServoDs5160,
                270,
                1,
                (-135, 135),
            )
        ),
        ActuatorPurpose.PITCH: ServoConnectionConfig(
            (
                ActuatorPurpose.PITCH,
                PiHeaderIdToBCM.THIRTY_THREE,
                ServoDs5160,
                270,
                1,
                (-130, 130),
            )
        ),
    },
    2: {
        ArmConnectionAttributes.PHYSICAL_LENGTH: SegmentLength,
        ActuatorPurpose.ROLL: ServoConnectionConfig(
            (
                ActuatorPurpose.ROLL,
                PiHeaderIdToBCM.THIRTY_FIVE,
                ServoDs5160,
                270,
                1,
                (-135, 135),
            )
        ),
        ActuatorPurpose.PITCH: ServoConnectionConfig(
            (
                ActuatorPurpose.PITCH,
                PiHeaderIdToBCM.THIRTY_SIX,
                ServoDs5160,
                270,
                1,
                (-130, 130),
            )
        ),
    },
    -1: {
        ArmConnectionAttributes.PHYSICAL_LENGTH: GripperLength,
        ActuatorPurpose.GRIPPER: ServoConnectionConfig(
            (
                ActuatorPurpose.GRIPPER,
                PiHeaderIdToBCM.FORTY,
                ServoDs3218,
                180,
                8,
                (-80, 0),
            )
        ),
    },
}


# Copied from the StructuralConfigsSi's configuration when generating mesh
SegmentLength = 200
GripperLength = 147
# servo_max_position should be configured according to which flavor of the arm was assembled
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

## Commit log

2023-03-01 control: added move_to_home_position, adjusted ps4 controller button mapping -- as L3 release
2023-03-01 control: expanded allowed pitch rotation range from abs(80) to abs(85), added validate_fk_ik
    [ato_3_seg.urdf]
2023-03-01 control: use pytest for sanity test
    [ato_3_seg.urdf]
2023-03-01 updated documentation
    restructured folders for python packaging
    [dragon_head.step]
2023-03-01 fixed issue vscode was not able to resolve the control package source code, added prefix ato_ to each package root folder
    [BOM.csv, ato_3_seg.urdf, dragon_head.step]
2023-03-04 mesh: larger base mount
2023-03-04 mesh: restructured gripper decorative into gripper using jaw, to prepare building another jaw based gripper
2023-03-12 mesh:
    support 270 degrees pitch
    tighten HornInnerOffset from 3 to 2, linter fixes
    [arm_configuration.py, arm_connection_config.py, arm_controller.py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]
2023-03-12 control: 270 pitch range
    [ato_3_seg.urdf]
2023-03-12 mesh: fixed structural issues for 270 degrees pitch
    [arm_connection_config.py, arm_controller.py, segment_configuration.py]
2023-03-12 mesh: added wire_tunnel_shortcut
2023-03-12 control: fixed issue in align_vectors and visualization
    [ato_3_seg.urdf]
2023-03-12 mesh: fixed pitch angle issue
    [generate_shelf_mesh.py, segment_configuration.py]
2023-03-15 control: evaluate_ik_cache forward_only within_reach
    [ato_3_seg.urdf]
2023-03-15 control: refactored to separate actuator_positions and joint_positions
2023-03-15 control: refactor to prepare multi threading
2023-03-15 control: ik_cache removed multiprocessing due to dependency thread safety
2023-03-20 control: added partial support for a 2 seg 180 deg arm
2023-03-20 control: refactored reset_trajectory_recording dictionary
    [arm_controller.py, ps4_joystick.py]
2023-03-20 mesh: fixed issue BoneSeparable triangle_holder was too talk to leave enough space for dragon head gripper
2023-03-20 urdf: added ato_2_seg_180_deg.urdf
    [ato_2_seg_180_deg.urdf, ato_3_seg_270_deg.urdf]
2023-03-26 control: improved cartesian, only update intended pose when it is allclose to expected pose, reset when no inputs given
    [arm_controller.py, arm_position.py, controller_enums.py]
2023-06-05 Tuning: Added local changes previously missed
    [arm_controller.py, arm_trajectory.py, ps4_joystick.py]
2023-09-04 Lhum/inverse kinematics (#11)
    * Adding inverse kinematics code
    It needs some debugging
    * Adding inverse kinematics code
    It needs some debugging
    * refactored inverse_kinematics_pinocchio
    cleaned up debugging code
    updated urdf files to add dummy object for pinocchio
    minor updates to env setup scripts
    * allow robot_wrapper.RobotWrapper.BuildFromURDF to fail
    -- so that ArmController class can instantiate without supporting files for the robot
    -- this would be expected during unit testing
    updated cicd scripts
    * removed ikpy_cache functionality
    * removed usage of ikpy
    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
    [ato_2_seg_180_deg.urdf, ato_3_seg_270_deg.urdf]
2023-11-19 Added another gripper: tri_sticks, working in progress
2023-11-19 Added pibullet visualization
    Tuned cartesian control
    To debug pitch issue at negative angles (upwards)
    [ato_2_seg_180_deg.urdf, ato_3_seg_270_deg.urdf]

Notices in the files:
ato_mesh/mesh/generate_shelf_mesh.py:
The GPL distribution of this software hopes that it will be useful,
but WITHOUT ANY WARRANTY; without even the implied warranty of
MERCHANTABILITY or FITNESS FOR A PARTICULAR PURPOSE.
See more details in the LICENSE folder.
